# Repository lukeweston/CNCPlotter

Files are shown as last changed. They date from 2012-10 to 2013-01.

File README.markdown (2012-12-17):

CNCPlotter

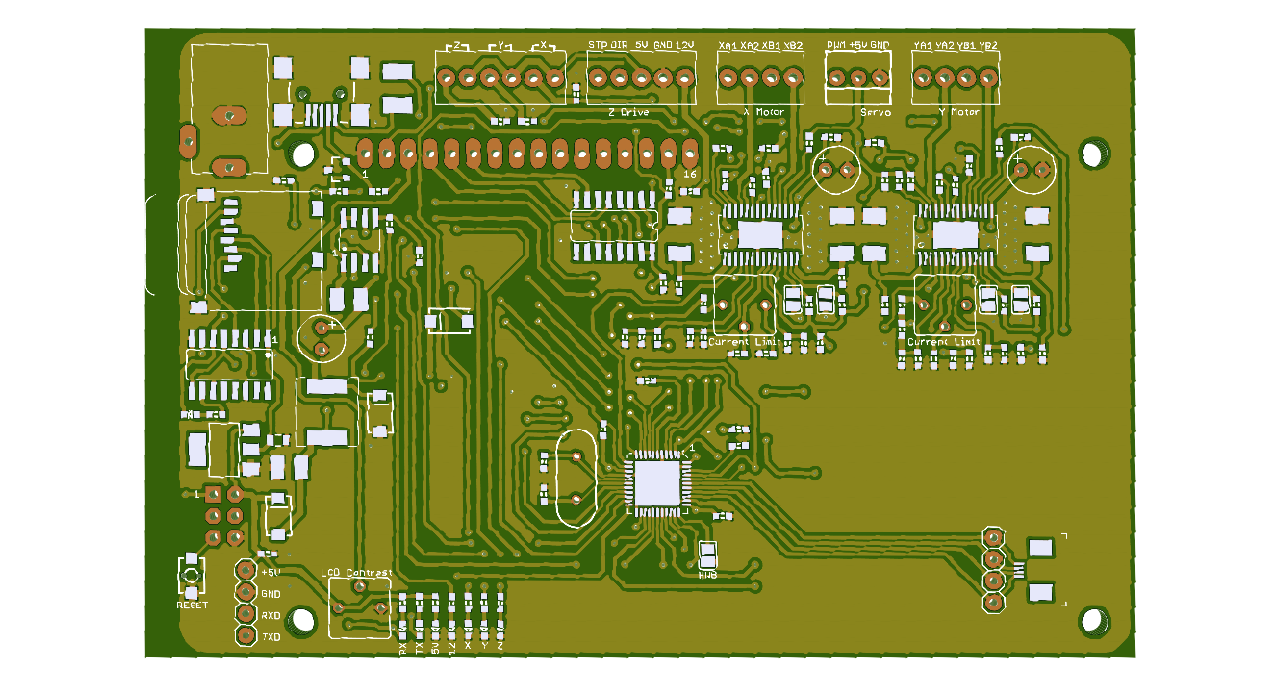
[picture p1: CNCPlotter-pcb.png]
 

The Freetronics CNCPlotter board is an Arduino-compatible embedded machine which incorporates two bipolar stepper motor drivers, suitable for CNC experiments and other
robotics and mechatronics applications.

The board incorporates the following hardware features:
 
- Atmel ATmega32U4 microcontroller, compatible with the Arduino Leonardo firmware, and USB connectivity to the PC. 
- 20x4 HD44780-compatible alphanumeric LCD display 
- Micro-SD card socket, for example usable for the execution of stored programs without connection to a PC. 
- Connector for a small (hobby RC aircraft style) servo motor 
- Two onboard DRV8811 bipolar stepper motor driver ICs 
- Inputs for three "limit" or "home" switches (or switches with any other kind of software-defined functionality!) 
- Connector for a cheap 4-wire resistive touchscreen, such as a Nintendo DS compatible touchscreen 
- Power supply input voltage range of 9-30V. (At least 1A current capacity is required to run the stepper motors.) 
- Output header for an optional third stepper motor driver IC, enabling three-axis CNC applications. 

Assuming you're using an Arduino Leonardo bootloader, the following is the mapping of Arduino pins to hardware functions.	

D0: UART RXD (not used, broken out to spare header) 	
D1: UART TXD (not used, broken out to spare header) 	
D2: LCD Strobe (Data loaded serially from AVR into 8-bit latch. Same as Pebble LCD hardware.) 	
D3: LCD Data 	
D4: LCD Clock 	
D5: Z-axis direction (not used in most cases) 	
D6: SD Card SPI chip select (active low). Standard SPI hardware (MOSI, MISO, SCK) used for SPI communications with SD card. 	
D7: Z-axis limit switch input (not used in most cases) 	
D8: Y-axis step signal 	
D9: Y-axis direction signal 	
D10: X-axis step signal 	
D11: X-axis direction signal 	
D12: Servo motor PWM position signal 	
D13: Z-axis step signal (not used usually) 	

A0: Touchscreen 1 	
A1: Touchscreen 2 	
A2: Touchscreen 3 	
A3: Touchscreen 4 	
A4: Y-axis limit switch input 	
A5: X-axis limit switch input

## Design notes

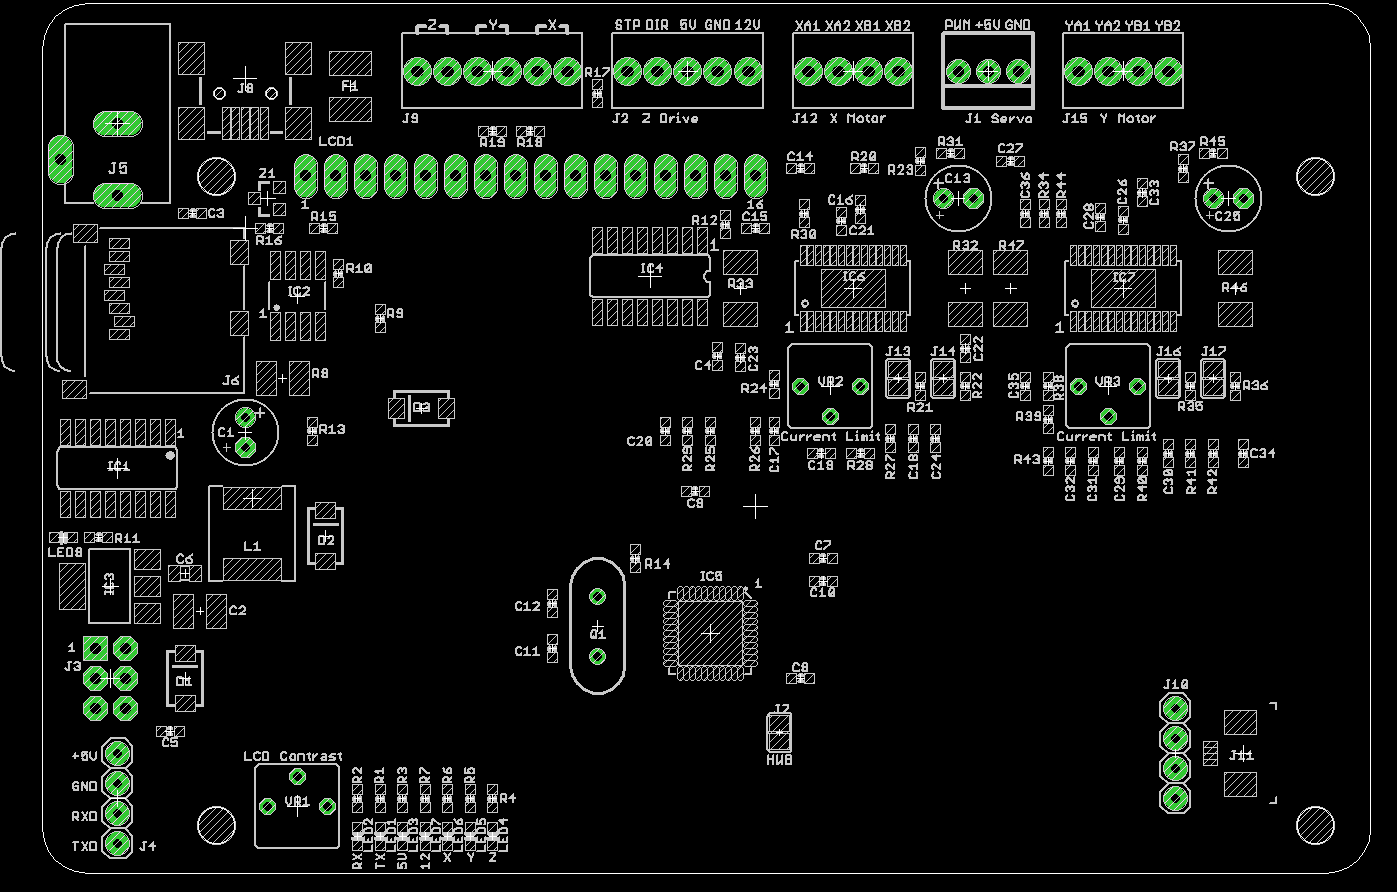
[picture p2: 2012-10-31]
CNCPlotter-placement.png

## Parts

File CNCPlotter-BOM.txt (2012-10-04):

R1, R2, R3, R4, R5, R6, R9, R11:								1k0, 0.1W, 0603 SMD, 5%
R13, R14, R17, R18, R19, R20, R21, R22, R23, R25, R30, R31, R34, R35, R36, R37, R39, R44, R45:	10k, 0.1W, 0603 SMD, 5%

R10:			3k0, 0.1W, 0603 SMD, 1%
R24, R38:		3k3, 0.1W, 0603 SMD, 5%
R12, R15, R16:		22R, 0.1W, 0603 SMD, 5%
R26, R27, R40, R41:	47k, 0.1W, 0603 SMD, 5%
R7, R29, R43:		4k7, 0.1W, 0603 SMD, 5%
R28, R42:		0 ohm, 0603 SMD
R8:			0.20 ohms, 0.5W, 1210 SMD, 5%. Eg. Digi-Key 73L5R20JCT-ND
R32, R33, R46, R47:	0.20 ohms, 1W, 2010 SMD, 1%. Eg. Digi-Key CSRN2010FKR200CT-ND

VR1, VR2, VR3:		CT6EP103 10k trimpot, eg. Digi-Key CT6EP103-ND

C1, C13, C25:		100 uF 35V Al electrolytic, through-hole, 2.5mm lead pitch / 6mm diameter. Eg. Digi-Key 399-6104-ND
C2:			47 uF ceramic, 1210 SMD. Eg. Digi-Key 445-1409-1-ND
C6:			10uF ceramic, 0805 SMD. Eg. Digi-Key 445-1371-1-ND
C3:			100 pF ceramic, 0603 SMD.
C9:			1 uF ceramic, 0603 SMD.
C11, C12:		22 pF ceramic, 0603 SMD.
C17, C18, C29, C30:	1 nF ceramic, 0603 SMD.

C14, C16, C21, C26, C28, C33:	220nF ceramic, 0603 SMD
C4, C5, C7, C8, C10, C15, C19, C20, C22, C23, C24, C27, C31, C32, C34, C35, C36: 100nF ceramic, 0603 SMD

D1, D2, D3:	CDBA120 Schottky diode, SMA package. Eg. Digi-Key 641-1014-1-ND
Z1:		PGB102ST23 ESD supressor, eg. Digi-Key F2596CT-ND 
Q1:		16 MHz crystal, through-hole HC-49US. Eg. Digi-Key 631-1108-ND
L1:		CR75 33uH power inductor, eg. Digi-Key 308-1539-1-ND
F1:		500mA PPTC, 1812 SMD package. Eg. Digi-Key 507-1361-1-ND

IC1:		MC14050, 16-SOIC package. Eg. Digi-Key MC14050BDGOS-ND
IC2:		MC34063 switching regulator, 8-SOIC package. Eg. Digi-Key 497-7852-1-ND
IC3:		LD1117S33C 3.3V regulator, SOT-223 package. Eg. Digi-Key 497-1241-1-ND
IC4:		74HC4094 shift register, 16-SOIC package. Eg. Digi-Key 568-1465-5-ND
IC5:		ATmega32U4 AVR microcontroller, 44-QFN package. Eg. Digi-Key ATMEGA32U4-MU-ND
IC6, IC7:	DRV8811 stepper motor driver, 28-HTSSOP. Eg. Digi-Key 296-24591-1-ND

LED1, LED7:		LED, green, 0603 SMD.
LED2, LED8:		LED, yellow, 0603 SMD.
LED3:			LED, blue, 0603 SMD.
LED4, LED5, LED6:	LED, red, 0603 SMD.

J1:		3-pin 0.1" pin header
J3:		2x3 0.1" pin header
J2:		5-pin 0.1" PCB-mount screw terminal block, eg. Digi-Key A98336-ND
J5:		2.1mm DC power jack, eg. Digi-Key CP-037A-ND
J6:		Micro-SD card socket, eg. Digi-Key 101-00660-68-6-1-ND
J8:		USB Mini-B socket, eg. Digi-Key H2959CT-ND
J9:		6-pin 0.1" PCB-mount screw terminal block, eg. Digi-Key A98337-ND
J11: 		4-pin 0.5mm SMD FFC ribbon connector, eg. Digi-Key 609-4328-1-ND
J12, J15:	4-pin 0.1" PCB-mount screw terminal block, eg. Digi-Key A98335-ND
J4:		NOT PLACED.
J10: 		NOT PLACED.

LCD1:		20x4 HD44780-compatible backlit LCD display module.
Same as Pebble, RAMPS Display Board, etc etc.
Also include appropriate headers (16-pin single-row 0.1", mating male/female pair) for LCD.

Also needed: 12V plugpack.

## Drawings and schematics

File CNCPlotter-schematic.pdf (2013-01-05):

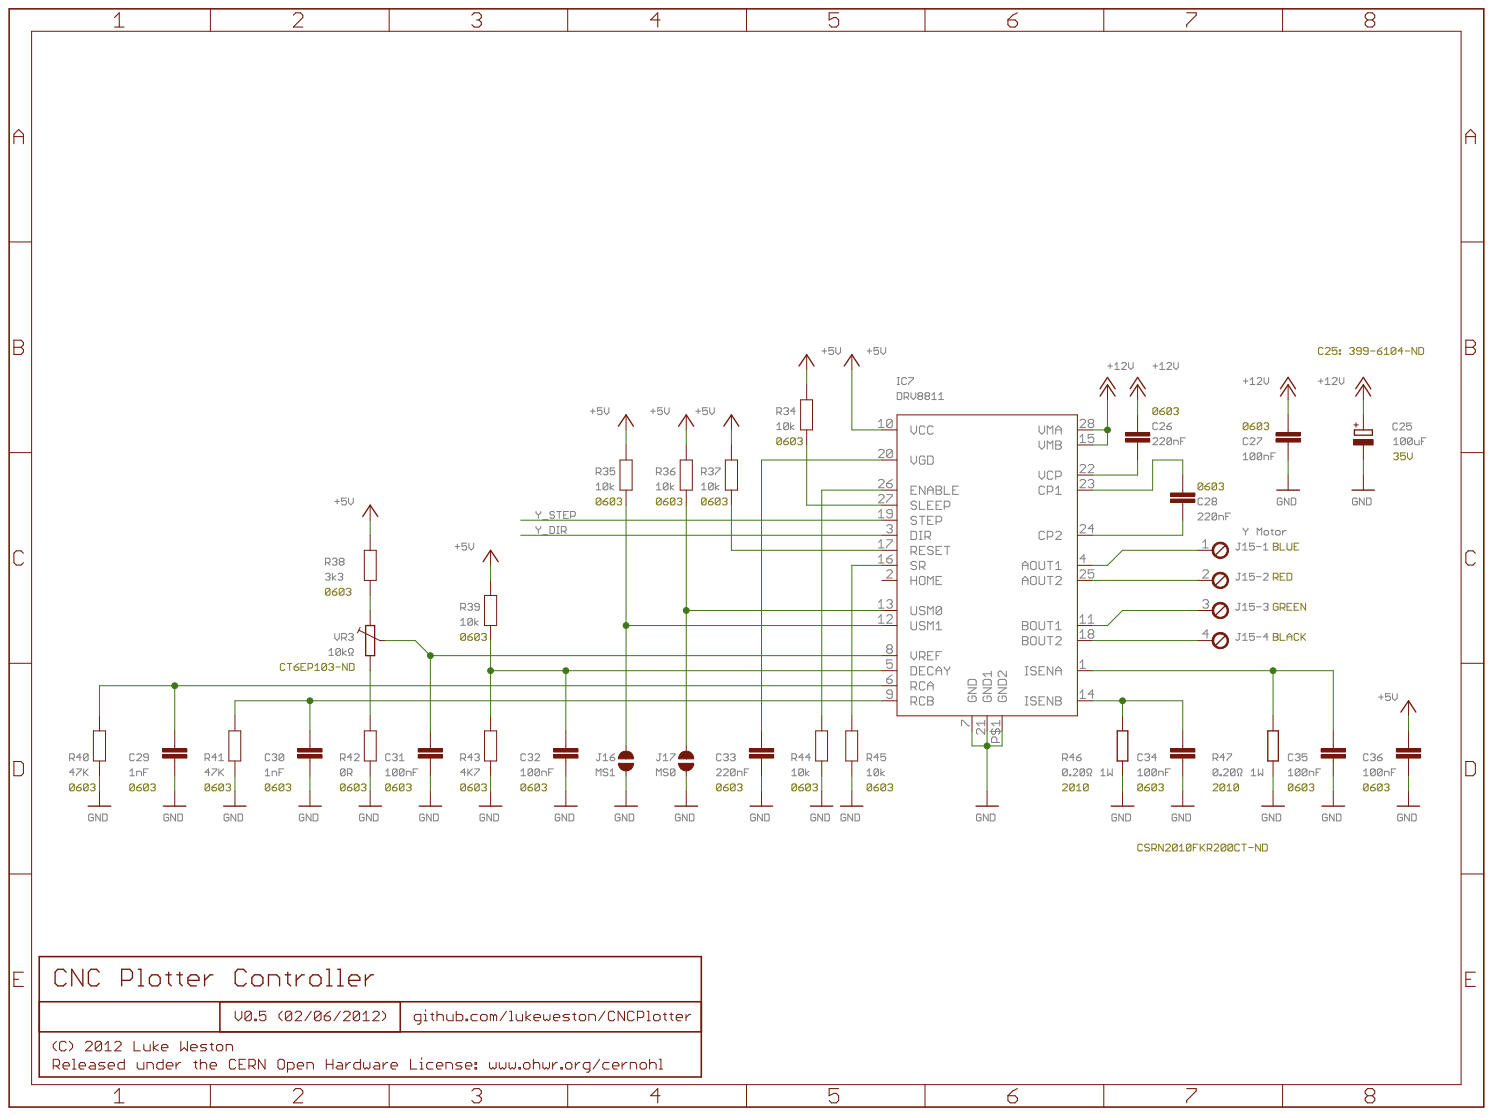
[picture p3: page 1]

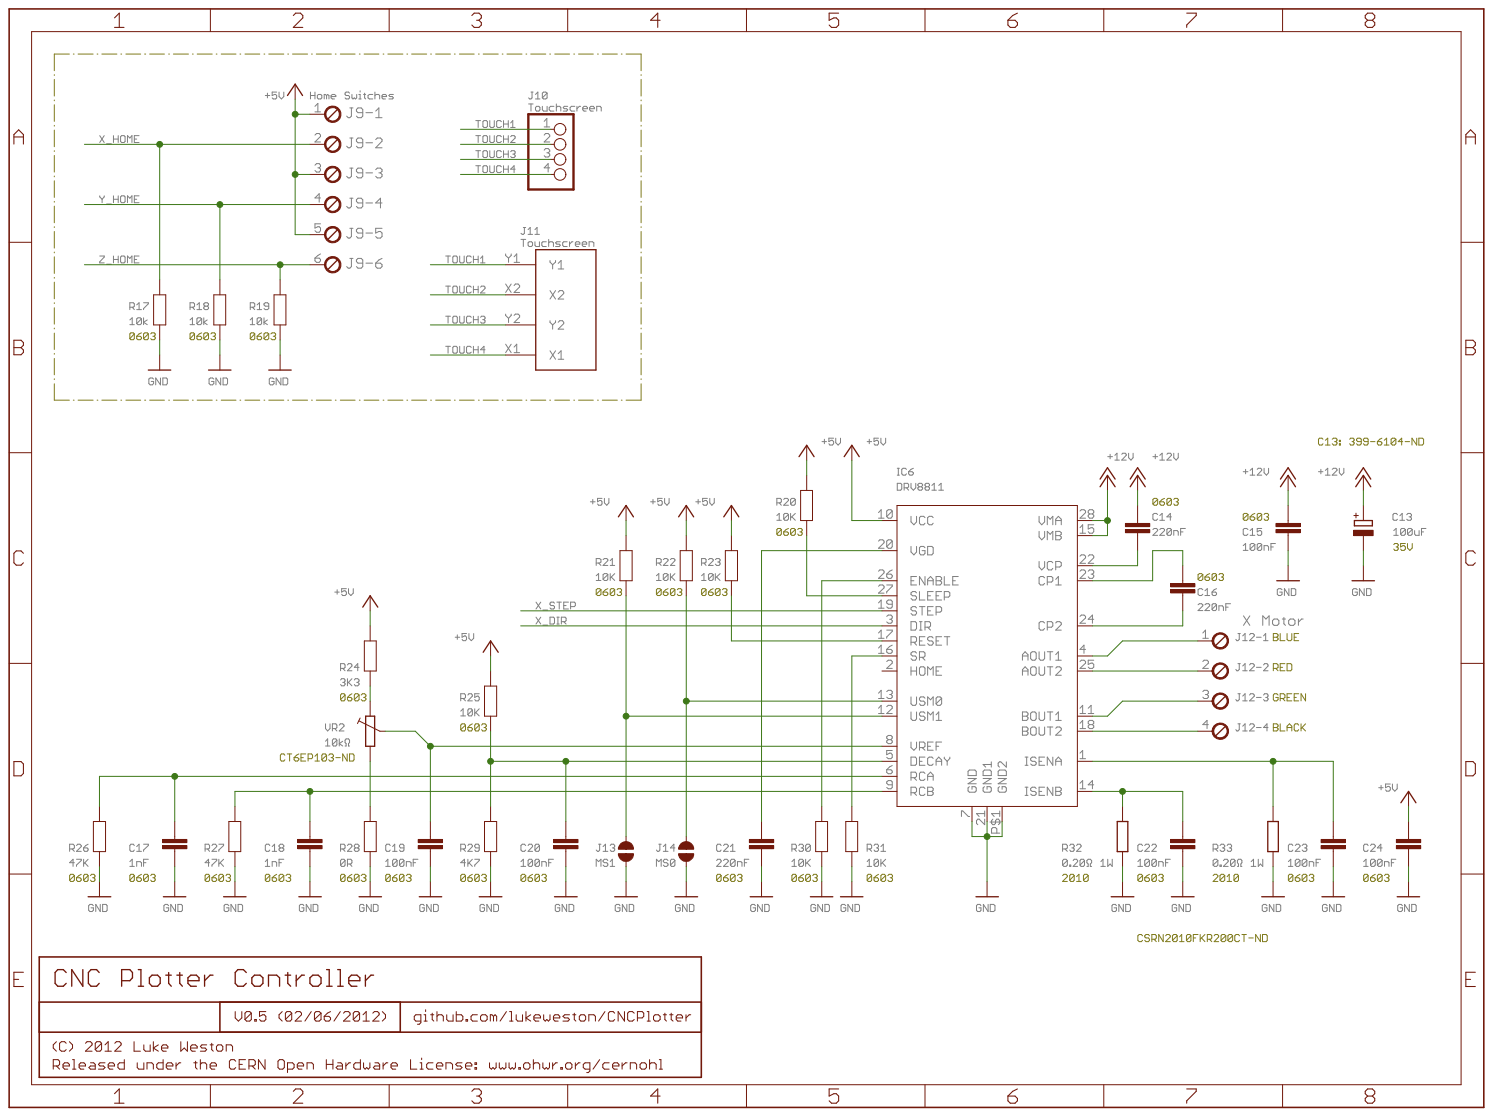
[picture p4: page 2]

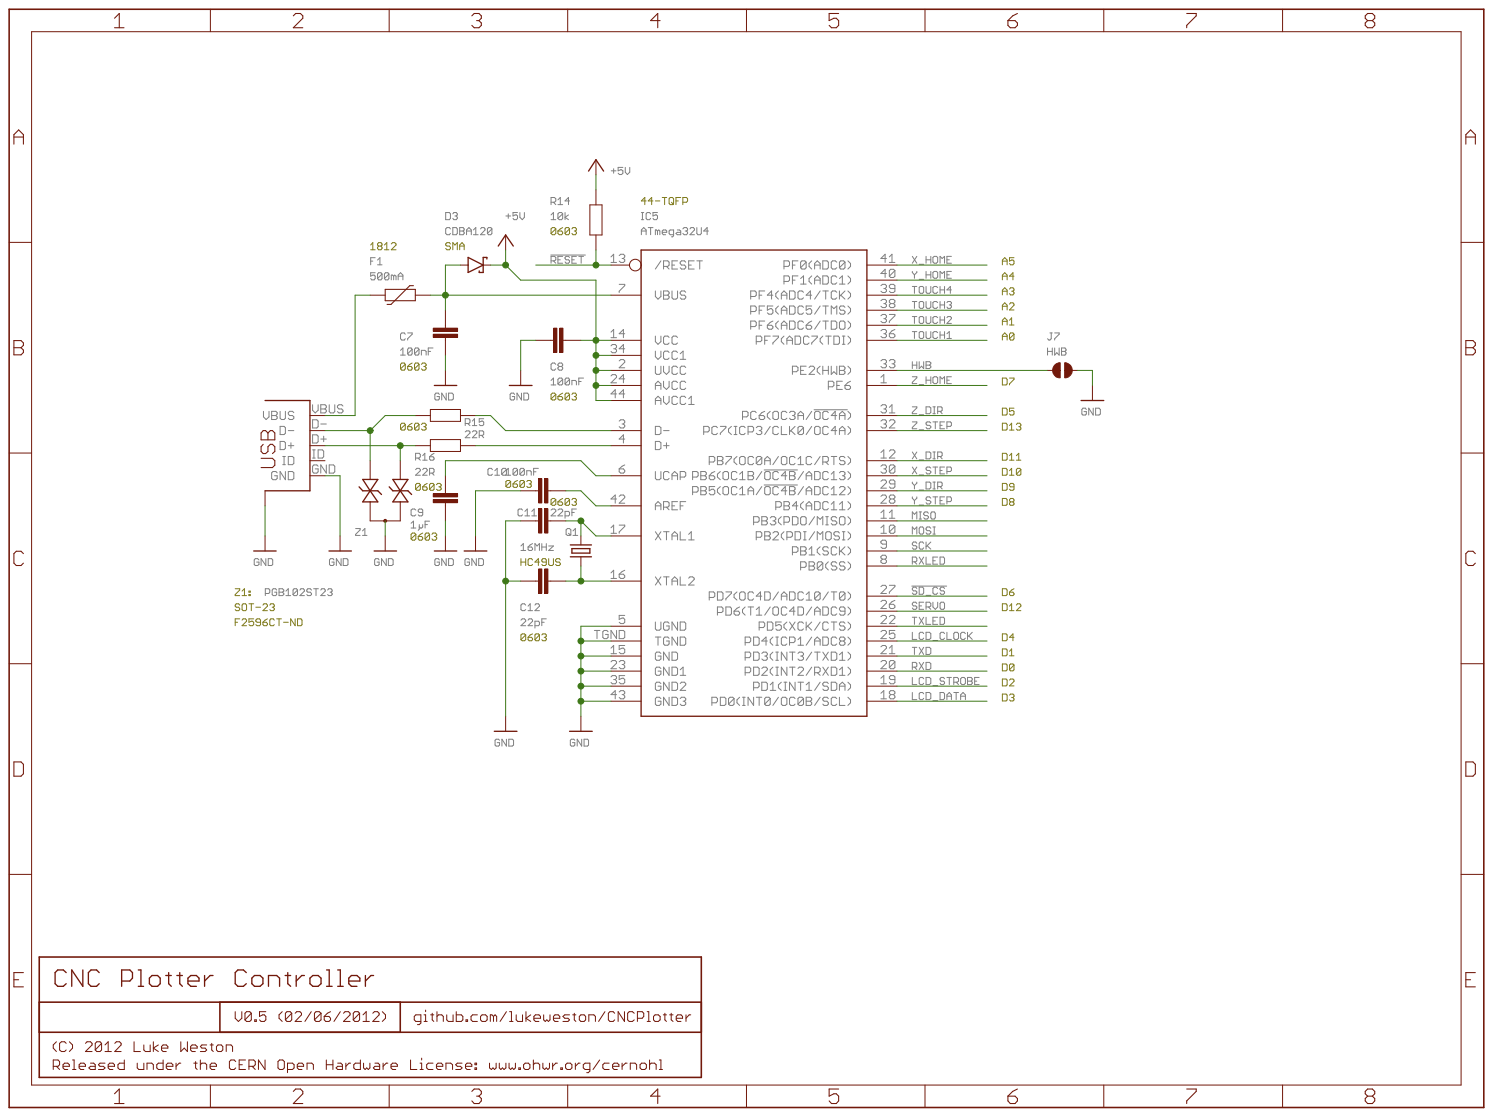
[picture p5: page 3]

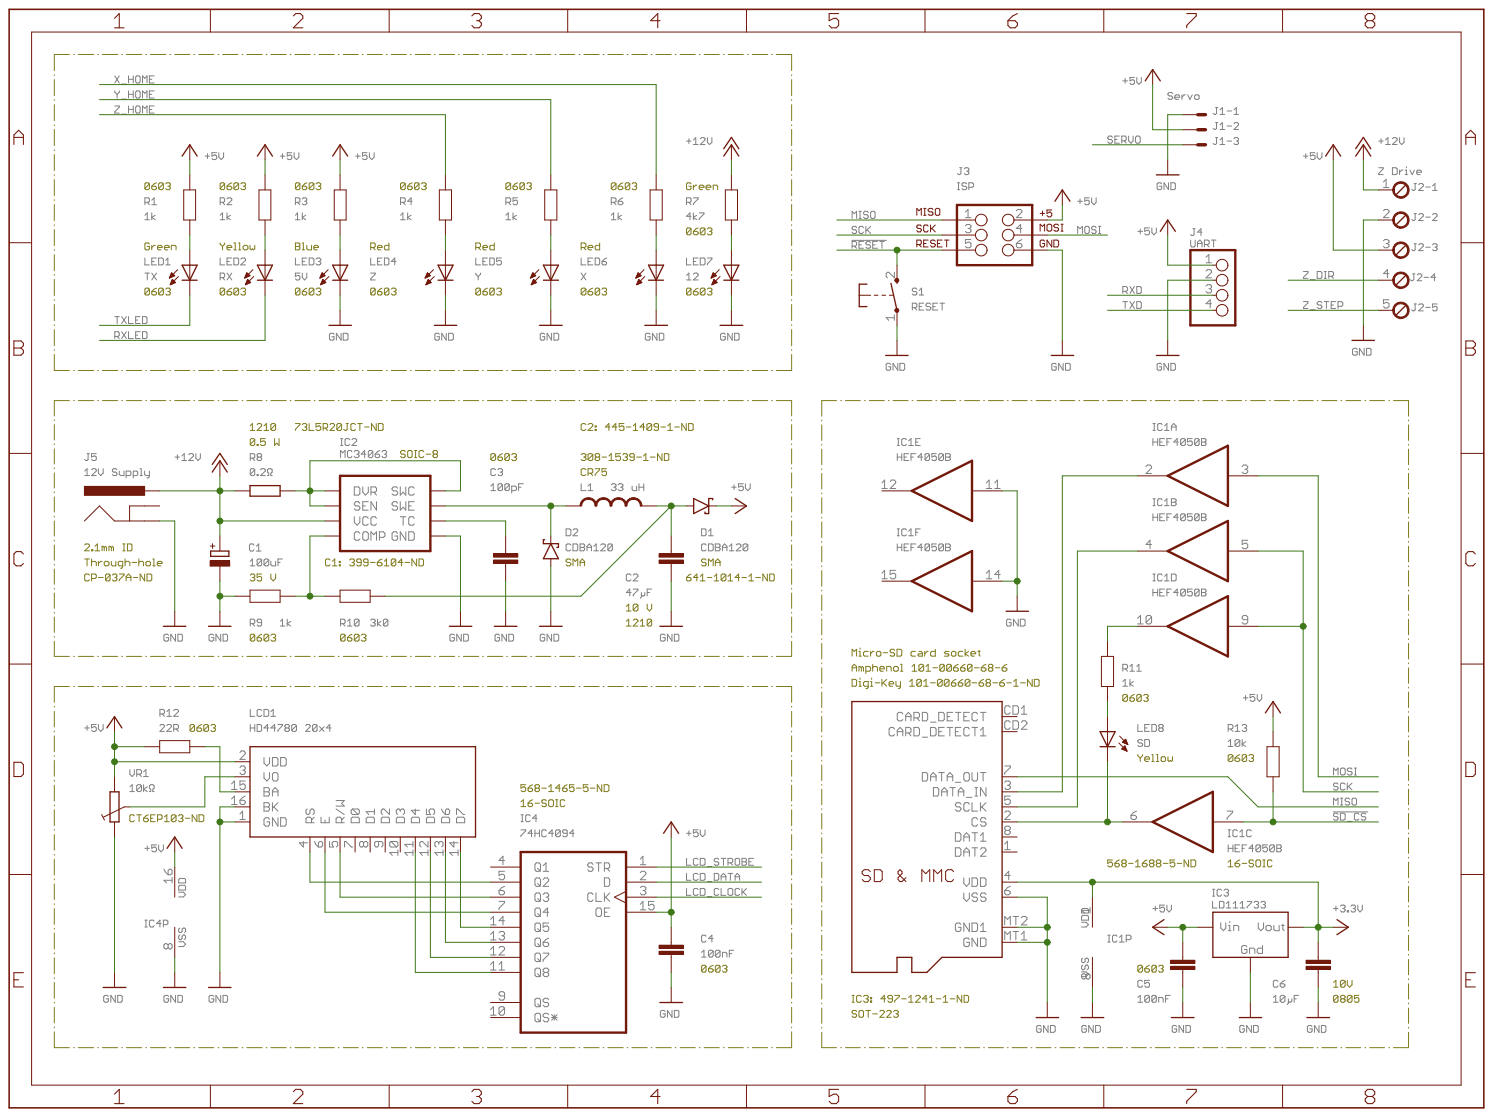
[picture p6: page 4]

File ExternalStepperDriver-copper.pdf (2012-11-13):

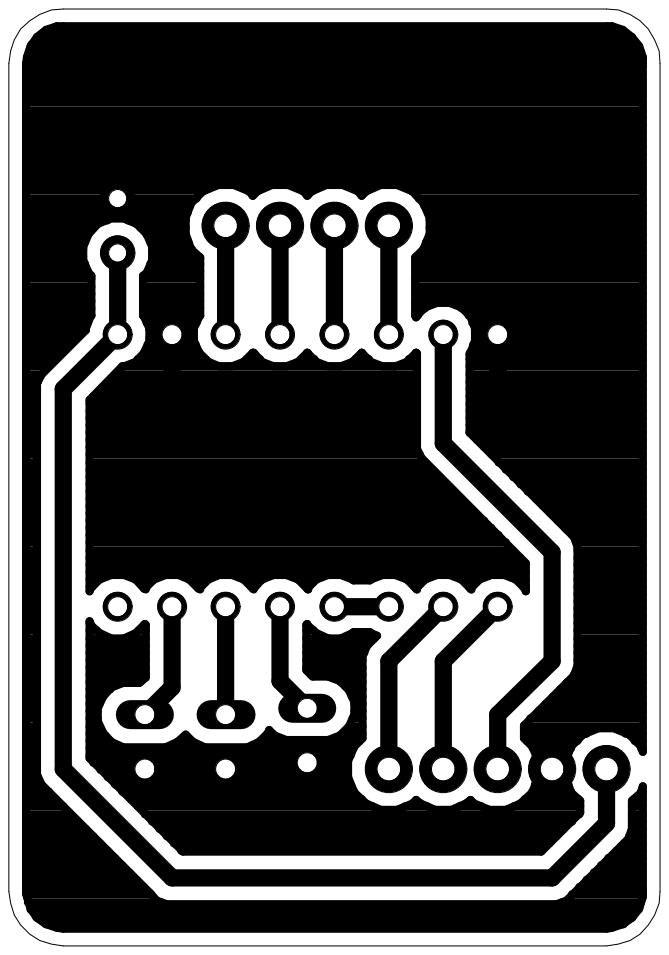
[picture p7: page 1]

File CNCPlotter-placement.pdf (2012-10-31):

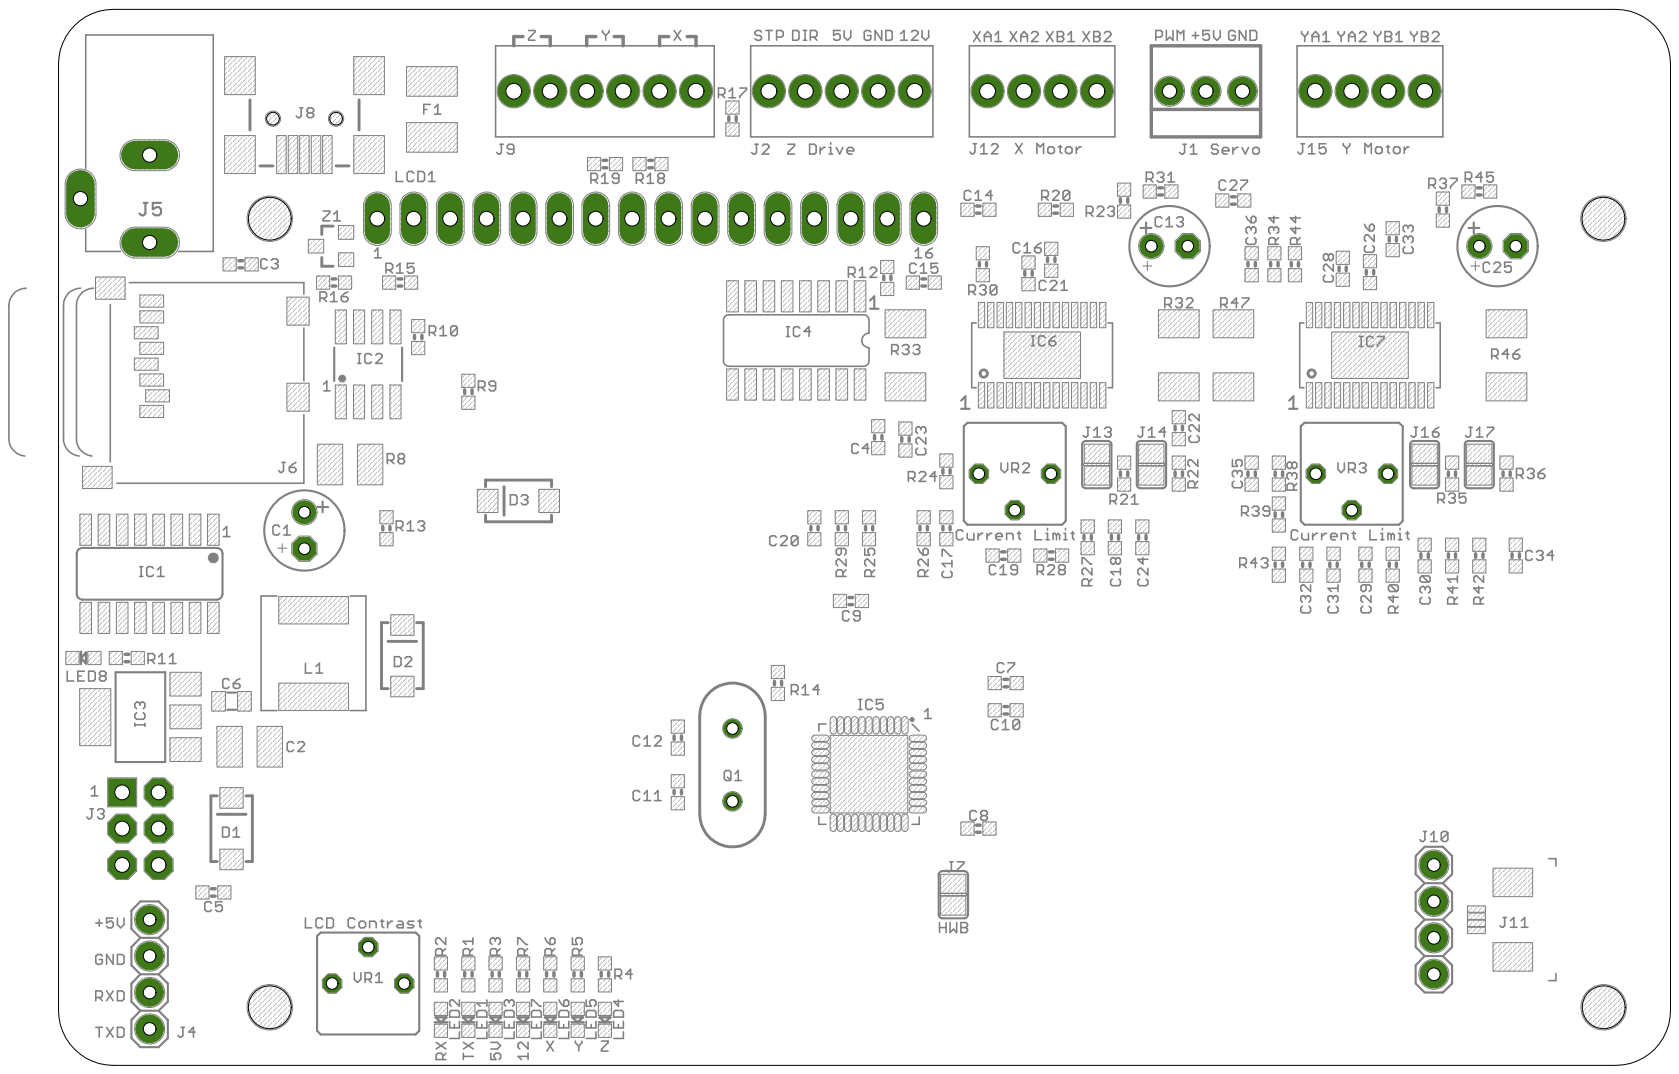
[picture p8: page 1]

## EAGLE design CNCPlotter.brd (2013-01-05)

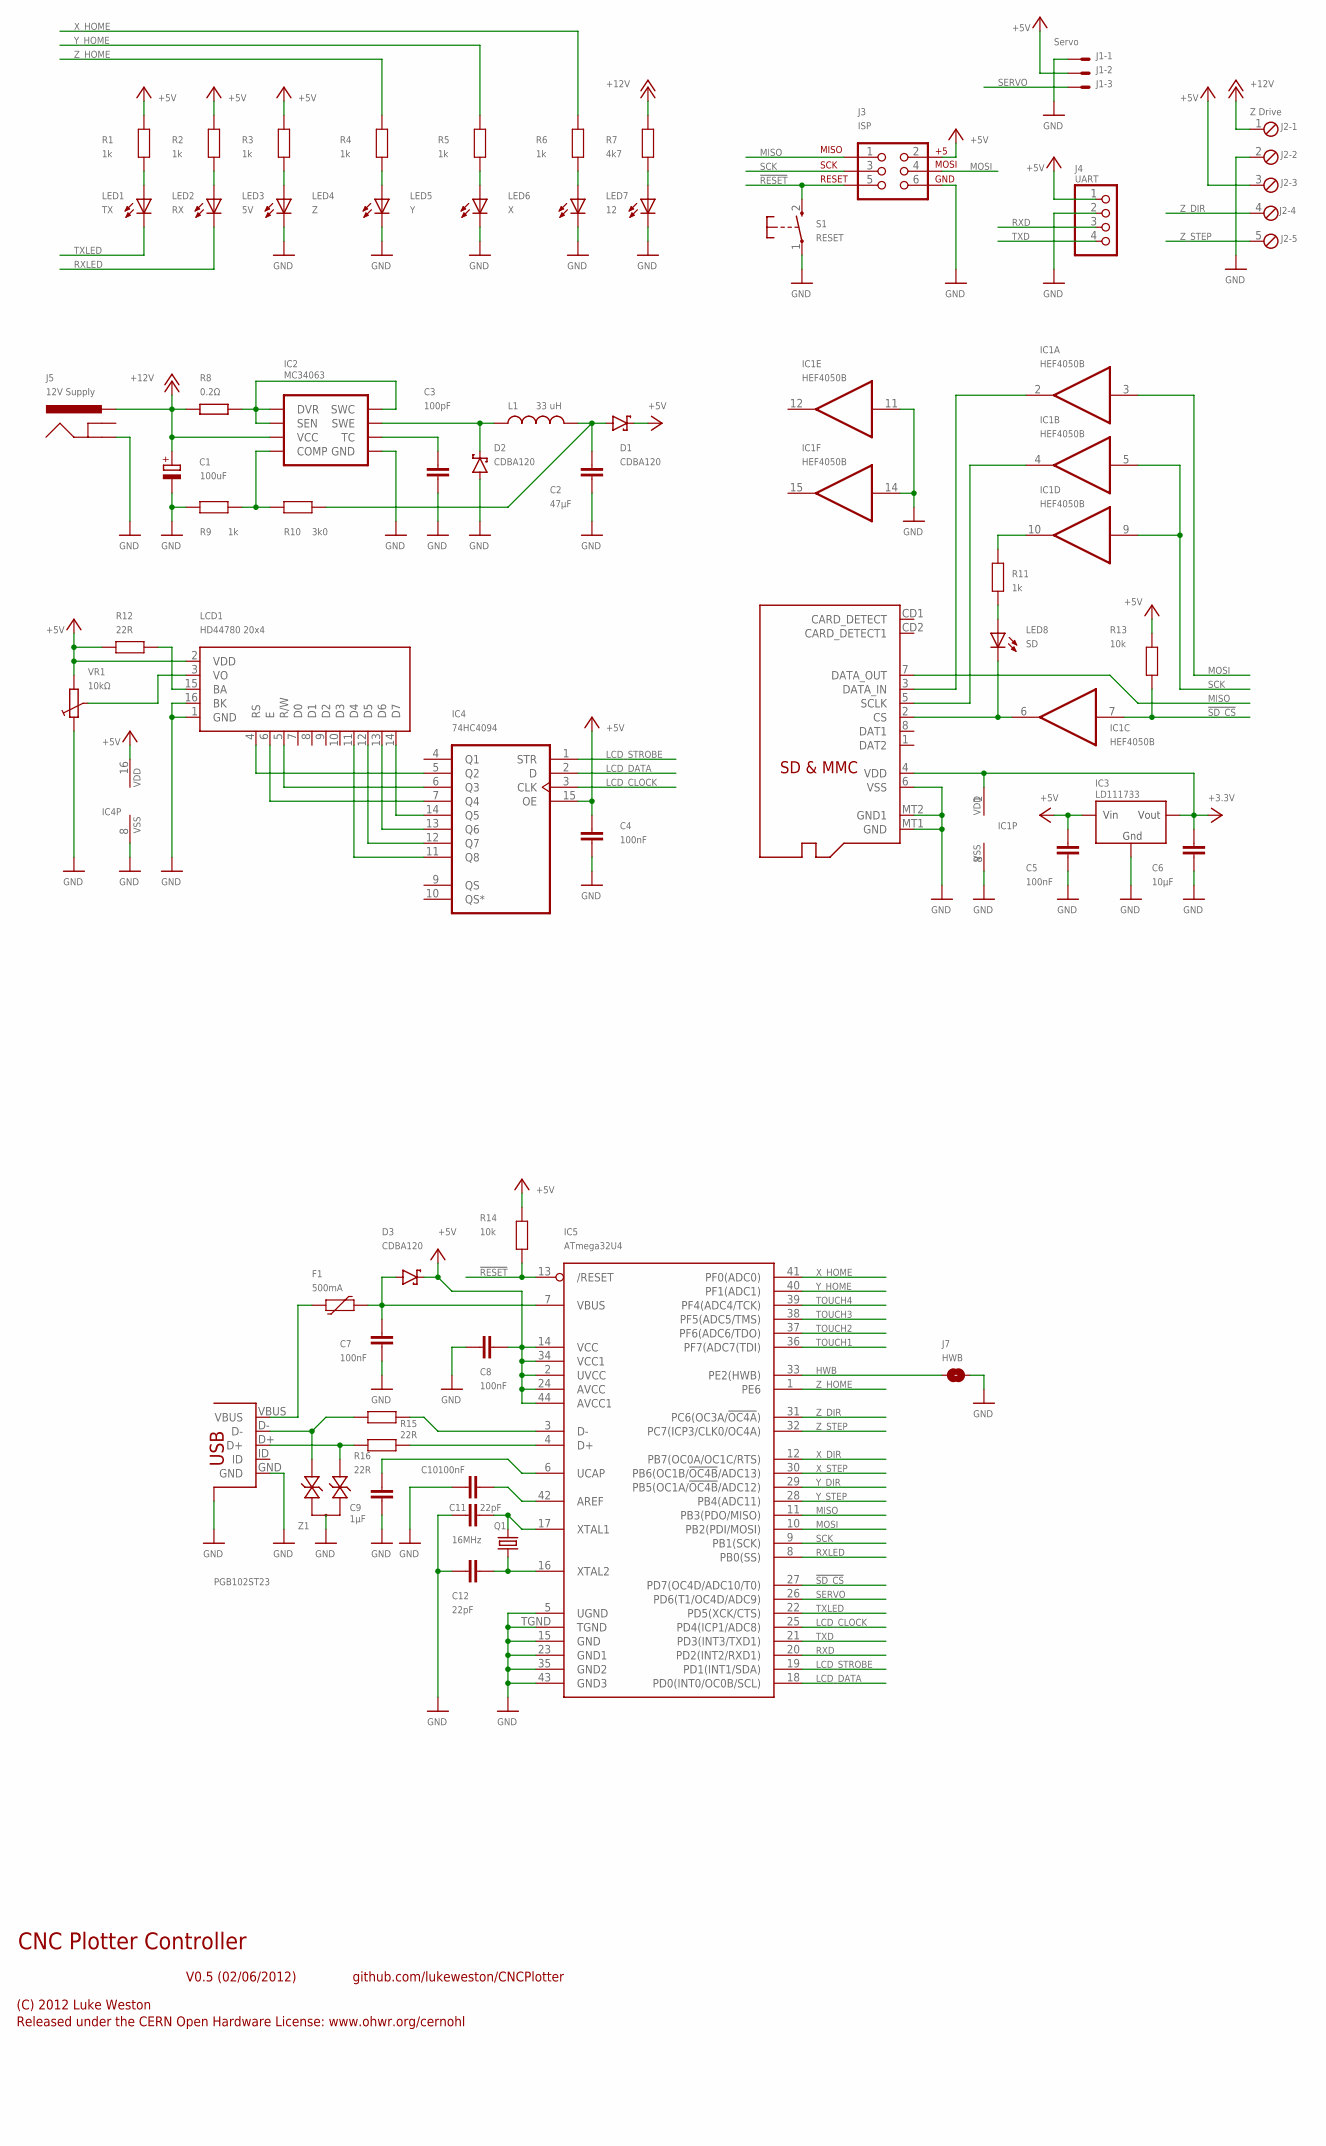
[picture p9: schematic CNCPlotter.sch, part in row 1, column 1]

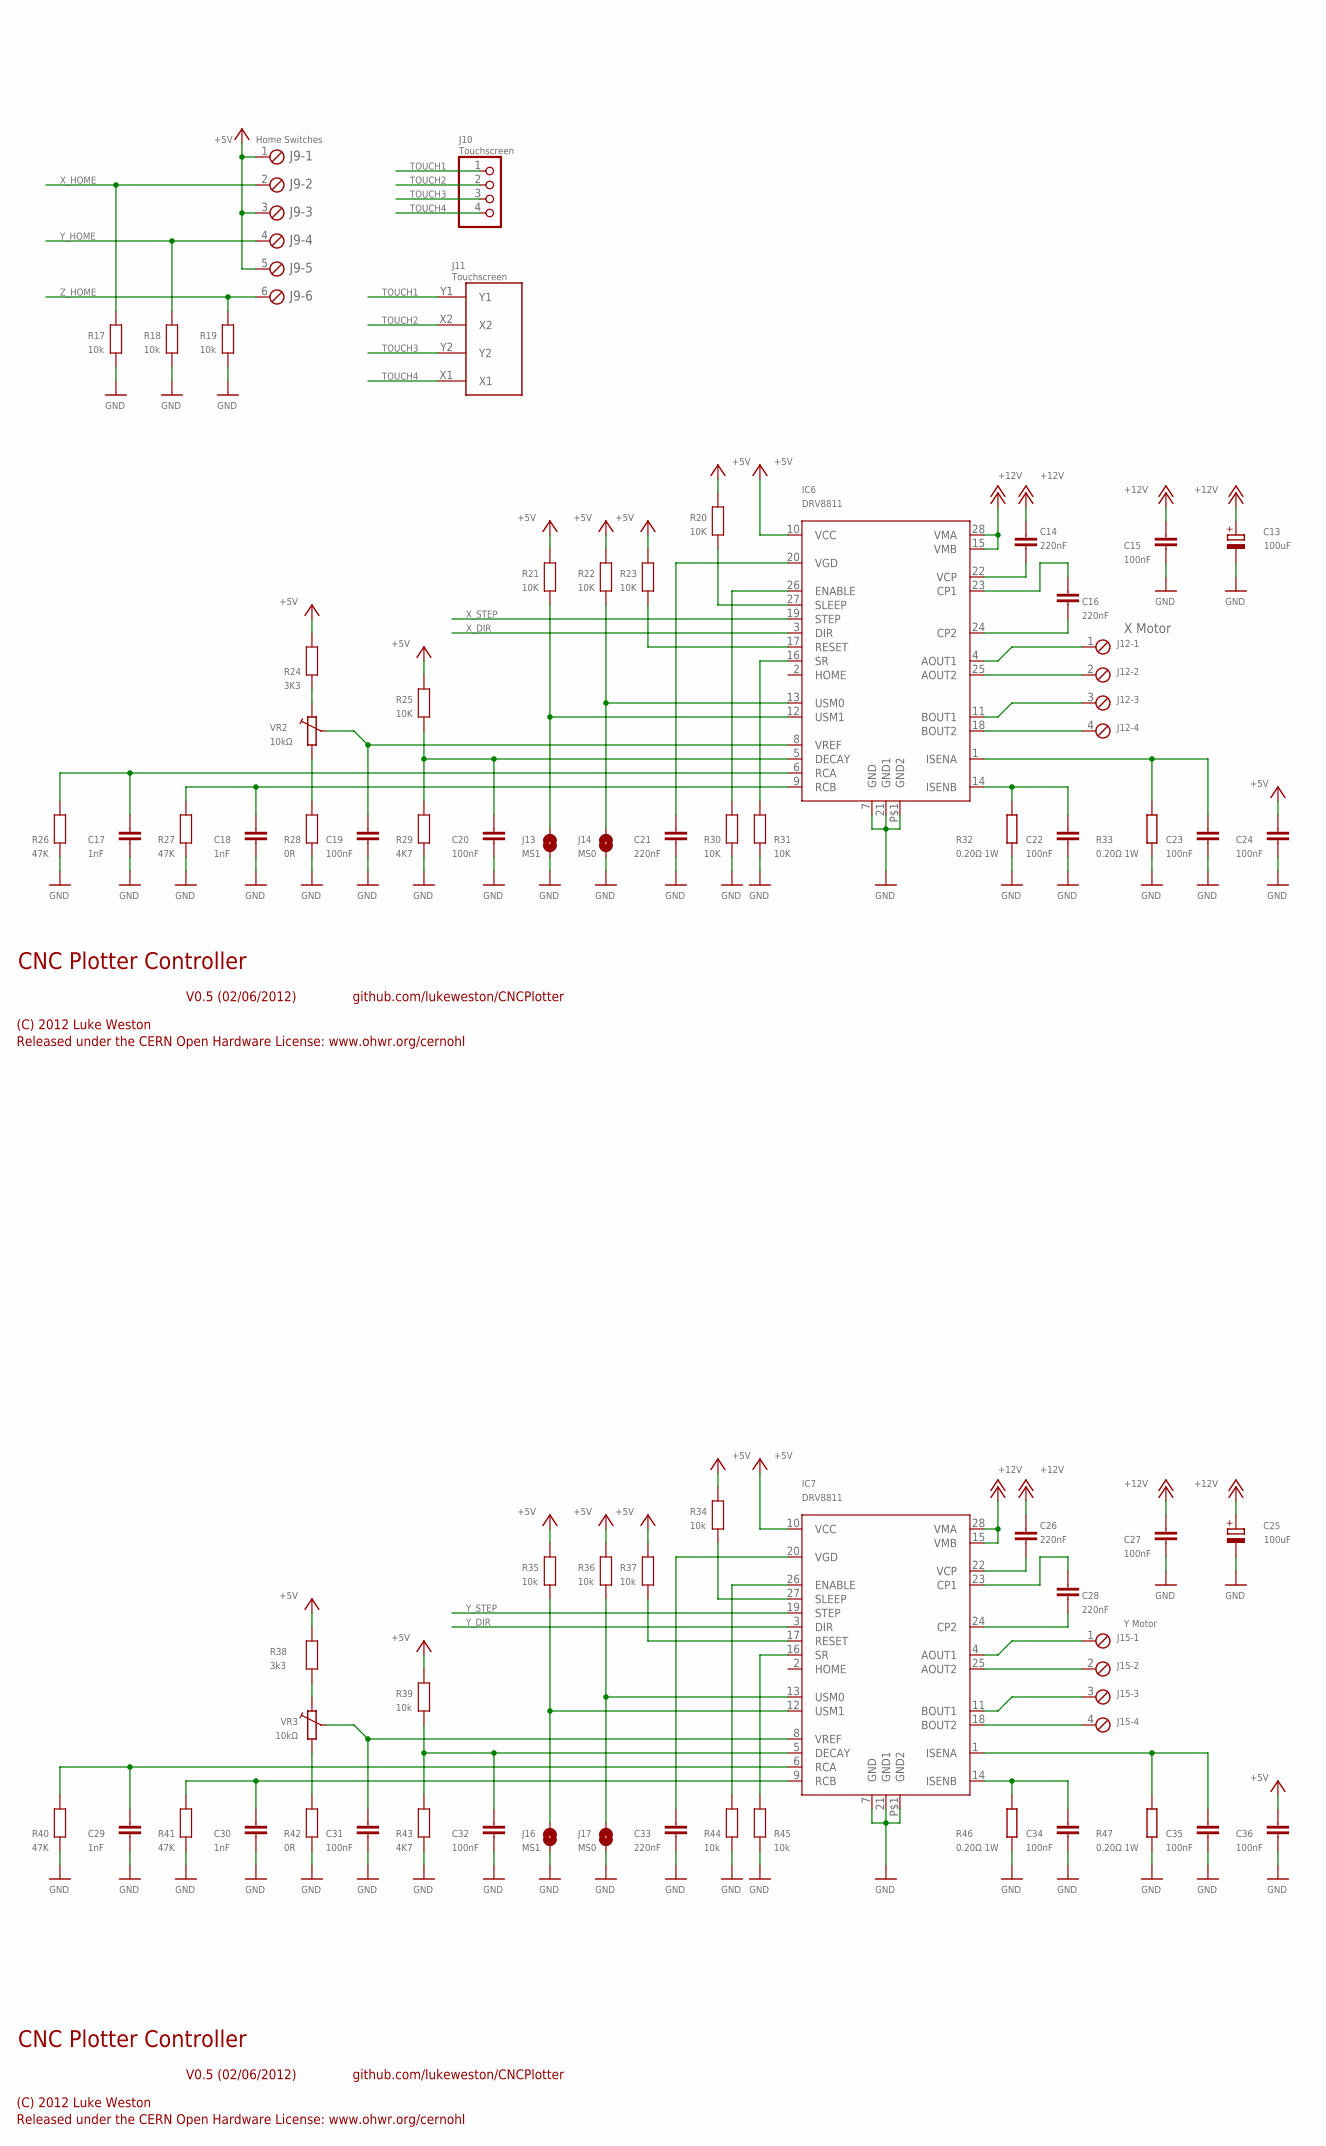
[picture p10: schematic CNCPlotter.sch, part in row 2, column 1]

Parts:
C1, C13, C25: 100uF; E2,5-6
C2: 47µF; C1210
C3: 100pF; 0603
C4, C5, C7, C8, C10, C15, C19, C20, C22, C23, C24, C27, C31, C32, C34, C35, C36: 100nF; 0603
C6: 10µF; 0805
C9: 1µF; 0603
C11, C12: 22pF; 0603
C14, C16, C21, C26, C28, C33: 220nF; 0603
C17, C18, C29, C30: 1nF; 0603
D1, D2, D3: CDBA120; SMA
F1: 500mA; 1812
IC1: HEF4050B; SO16
IC2: MC34063; SO08
IC3: LD111733; SOT223
IC4: 74HC4094; SO16@1
IC5: ATmega32U4; QFN-44N
IC6, IC7: DRV8811; HTSSOP28
J1: Servo; 22-23-2031
J2: Z Drive; 5POL254
J3: ISP; 2X3-NS
J4: UART; 1X04
J5: 12V Supply; POWER_JACK_SLOT
J6: MicroSD Card; ADAFRUIT_MICROSD
J7: HWB; SJ
J8: USB; USB-MINIB-FT
J9: Home Switches; 6POL254
J10: Touchscreen; 1X04
J11: Touchscreen; DS_TOUCH_CONNECTOR
J12: X Motor; 4POL254
J13, J16: MS1; SJ
J14, J17: MS0; SJ
J15: Y Motor; 4POL254
L1: 33 uH; CR75
LCD1: HD44780 20x4; HDM20416L
LED1: TX; LED-0603
LED2: RX; LED-0603
LED3: 5V; LED-0603
LED4: Z; LED-0603
LED5: Y; LED-0603
LED6: X; LED-0603
LED7: 12; LED-0603
LED8: SD; LED-0603
Q1: 16MHz; HC49US
R1, R2, R3, R4, R5, R6, R9, R11: 1k; 0603
R7: 4k7; 0603
R8: 0.2Ω; R1210
R10: 3k0; 0603
R12, R15, R16: 22R; 0603
R13, R14, R17, R18, R19, R34, R35, R36, R37, R39, R44, R45: 10k; 0603
R20, R21, R22, R23, R25, R30, R31: 10K; 0603
R24: 3K3; 0603
R26, R27, R40, R41: 47K; 0603
R28, R42: 0R; 0603
R29, R43: 4K7; 0603
R32, R33, R46, R47: 0.20Ω 1W; R2010
R38: 3k3; 0603
S1: RESET; TACTILE_SWITCH_SMD_2PIN_TINY
VR1, VR2, VR3: 10kΩ; CT6
Z1: PGB102ST23; SOT23-3

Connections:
!RESET: IC5.13 (/RESET), J3.5, R14.1, S1.2 (S)
!SD_CS: IC1.7 (I), IC5.27 (PD7(OC4D/ADC10/T0)), R13.1
+5V: C4.1, C5.1, C8.2, C24.1, C36.1, D1.K, D3.K, IC3.3 (VIN), IC4.15 (OE), IC4.16 (VDD), IC5.2 (UVCC), IC5.14 (VCC), IC5.24 (AVCC), IC5.34 (VCC1), IC5.44 (AVCC1), IC6.10 (VCC), IC7.10 (VCC), J1.2, J2.3, J3.2, J4.1, J9.1, J9.3, J9.5, LCD1.2 (VDD), R1.2, R2.2, R3.2, R12.2, R13.2, R14.2, R20.2, R21.2, R22.2, R23.2, R24.2, R25.2, R34.2, R35.2, R36.2, R37.2, R38.2, R39.2, VR1.A
+12V: C1.+, C13.+, C14.1, C15.1, C25.+, C26.1, C27.1, IC2.6 (VCC), IC6.15 (VMB), IC6.28 (VMA), IC7.15 (VMB), IC7.28 (VMA), J2.1, J5.PWR, R7.2, R8.1
FOO: IC1.6 (O), J6.2 (CS), LED8.C
GND: C1.-, C2.2, C3.2, C4.2, C5.2, C6.2, C7.2, C8.1, C9.1, C10.1, C11.1, C12.1, C13.-, C15.2, C17.2, C18.2, C19.2, C20.2, C21.2, C22.2, C23.2, C24.2, C25.-, C27.2, C29.2, C30.2, C31.2, C32.2, C33.2, C34.2, C35.2, C36.2, D2.A, IC1.8 (VSS), IC1.11 (I), IC1.14 (I), IC2.4 (GND), IC3.1 (GND), IC4.8 (VSS), IC5.5 (UGND), IC5.15 (GND), IC5.23 (GND1), IC5.35 (GND2), IC5.43 (GND3), IC5.TGND, IC6.7 (GND), IC6.21 (GND1), IC6.P$1 (GND2), IC7.7 (GND), IC7.21 (GND1), IC7.P$1 (GND2), J1.1, J2.2, J3.6, J4.2, J5.GND, J6.6 (VSS), J6.MT1 (GND), J6.MT2 (GND1), J7.1, J8.GND, J8.SH1 (SH$1), J8.SH2 (SH$1), J8.SH3 (SH$1), J8.SH4 (SH$1), J13.1, J14.1, J16.1, J17.1, LCD1.1 (GND), LCD1.16 (BK), LED3.C, LED4.C, LED5.C, LED6.C, LED7.C, R9.2, R17.2, R18.2, R19.2, R26.1, R27.1, R28.1, R29.1, R30.1, R31.1, R32.1, R33.1, R40.1, R41.1, R42.1, R43.1, R44.1, R45.1, R46.1, R47.1, S1.1, VR1.E, Z1.3
HWB: IC5.33 (PE2(HWB)), J7.2
LCD_CLOCK: IC4.3 (CLK), IC5.25 (PD4(ICP1/ADC8))
LCD_DATA: IC4.2 (D), IC5.18 (PD0(INT0/OC0B/SCL))
LCD_STROBE: IC4.1 (STR), IC5.19 (PD1(INT1/SDA))
MISO: IC5.11 (PB3(PDO/MISO)), J3.1, J6.7 (DATA_OUT)
MOSI: IC1.3 (I), IC5.10 (PB2(PDI/MOSI)), J3.4
MOSI_3.3V: IC1.2 (O), J6.3 (DATA_IN)
unnamed: IC7.4 (AOUT1), J15.1
unnamed: F1.1, J8.VBUS
unnamed: IC6.4 (AOUT1), J12.1
unnamed: IC7.18 (BOUT2), J15.4
unnamed: IC7.11 (BOUT1), J15.3
unnamed: IC7.25 (AOUT2), J15.2
unnamed: C28.2, IC7.24 (CP2)
unnamed: C28.1, IC7.23 (CP1)
unnamed: C26.2, IC7.22 (VCP)
unnamed: C33.1, IC7.20 (VGD)
unnamed: C10.2, IC5.42 (AREF)
unnamed: LED4.A, R4.1
unnamed: C35.1, IC7.1 (ISENA), R47.2
unnamed: C34.1, IC7.14 (ISENB), R46.2
unnamed: C32.1, IC7.5 (DECAY), R39.1, R43.2
unnamed: C29.1, IC7.6 (RCA), R40.2
unnamed: C16.2, IC6.24 (CP2)
unnamed: C16.1, IC6.23 (CP1)
unnamed: IC6.16 (SR), R31.2
unnamed: C30.1, IC7.9 (RCB), R41.2
unnamed: IC6.18 (BOUT2), J12.4
unnamed: IC6.11 (BOUT1), J12.3
unnamed: IC6.25 (AOUT2), J12.2
unnamed: C14.2, IC6.22 (VCP)
unnamed: C20.1, IC6.5 (DECAY), R25.1, R29.2
unnamed: C21.1, IC6.20 (VGD)
unnamed: C17.1, IC6.6 (RCA), R26.2
unnamed: C9.2, IC5.6 (UCAP)
unnamed: LED3.A, R3.1
unnamed: LED2.A, R2.1
unnamed: LED1.A, R1.1
unnamed: IC2.1 (SWC), IC2.7 (SEN), IC2.8 (DVR), R8.2
unnamed: J8.D+, R16.2, Z1.1
unnamed: J8.D-, R15.2, Z1.2
unnamed: C11.2, IC5.17 (XTAL1), Q1.2
unnamed: C12.2, IC5.16 (XTAL2), Q1.1
unnamed: IC5.4 (D+), R16.1
unnamed: IC5.3 (D-), R15.1
unnamed: LED5.A, R5.1
unnamed: C7.1, D3.A, F1.2, IC5.7 (VBUS)
unnamed: LED6.A, R6.1
unnamed: LED7.A, R7.1
unnamed: C3.1, IC2.3 (TC)
unnamed: IC2.5 (COMP), R9.1, R10.2
unnamed: D2.K, IC2.2 (SWE), L1.P$1 (1)
unnamed: C23.1, IC6.1 (ISENA), R33.2
unnamed: C22.1, IC6.14 (ISENB), R32.2
unnamed: C18.1, IC6.9 (RCB), R27.2
unnamed: IC6.27 (SLEEP), R20.1
unnamed: IC4.5 (Q2), LCD1.4 (RS)
unnamed: IC4.6 (Q3), LCD1.5 (R/W)
unnamed: IC4.7 (Q4), LCD1.6 (E)
unnamed: IC4.11 (Q8), LCD1.11 (D4)
unnamed: IC4.12 (Q7), LCD1.12 (D5)
unnamed: IC4.13 (Q6), LCD1.13 (D6)
unnamed: IC4.14 (Q5), LCD1.14 (D7)
unnamed: IC6.17 (RESET), R23.1
unnamed: LCD1.3 (VO), VR1.S
unnamed: LCD1.15 (BA), R12.1
unnamed: R24.1, VR2.E
unnamed: R28.2, VR2.A
unnamed: LED8.A, R11.1
unnamed: IC1.10 (O), R11.2
unnamed: C19.1, IC6.8 (VREF), VR2.S
unnamed: IC6.26 (ENABLE), R30.2
unnamed: IC6.12 (USM1), J13.2, R21.1
unnamed: IC6.13 (USM0), J14.2, R22.1
unnamed: IC7.27 (SLEEP), R34.1
unnamed: IC7.17 (RESET), R37.1
unnamed: R38.1, VR3.E
unnamed: R42.2, VR3.A
unnamed: C31.1, IC7.8 (VREF), VR3.S
unnamed: IC7.26 (ENABLE), R44.2
unnamed: IC7.12 (USM1), J16.2, R35.1
unnamed: IC7.13 (USM0), J17.2, R36.1
unnamed: IC7.16 (SR), R45.2
REG_5V: C2.1, D1.A, L1.P$2 (2), R10.1
RXD: IC5.20 (PD2(INT2/RXD1)), J4.3
RXLED: IC5.8 (PB0(SS)), LED2.C
SCK: IC1.5 (I), IC1.9 (I), IC5.9 (PB1(SCK)), J3.3
SCK_3.3V: IC1.4 (O), J6.5 (SCLK)
SERVO: IC5.26 (PD6(T1/OC4D/ADC9)), J1.3
TOUCH1: IC5.36 (PF7(ADC7(TDI)), J10.1, J11.Y1
TOUCH2: IC5.37 (PF6(ADC6/TDO)), J10.2, J11.X2
TOUCH3: IC5.38 (PF5(ADC5/TMS)), J10.3, J11.Y2
TOUCH4: IC5.39 (PF4(ADC4/TCK)), J10.4, J11.X1
TXD: IC5.21 (PD3(INT3/TXD1)), J4.4
TXLED: IC5.22 (PD5(XCK/CTS)), LED1.C
VDD: C6.1, IC1.1 (VDD), IC3.2 (VOUT), J6.4 (VDD)
X_DIR: IC5.12 (PB7(OC0A/OC1C/RTS)), IC6.3 (DIR)
X_HOME: IC5.41 (PF0(ADC0)), J9.2, R6.2, R17.1
X_STEP: IC5.30 (PB6(OC1B/!OC4B!/ADC13)), IC6.19 (STEP)
Y_DIR: IC5.29 (PB5(OC1A/!OC4B!/ADC12)), IC7.3 (DIR)
Y_HOME: IC5.40 (PF1(ADC1)), J9.4, R5.2, R18.1
Y_STEP: IC5.28 (PB4(ADC11)), IC7.19 (STEP)
Z_DIR: IC5.31 (PC6(OC3A/!OC4A!)), J2.4
Z_HOME: IC5.1 (PE6), J9.6, R4.2, R19.1
Z_STEP: IC5.32 (PC7(ICP3/CLK0/OC4A)), J2.5

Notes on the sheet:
CNC Plotter Controller
V0.5 (02/06/2012)
(C) 2012 Luke Weston
Released under the CERN Open Hardware License: www.ohwr.org/cernohl
github.com/lukeweston/CNCPlotter

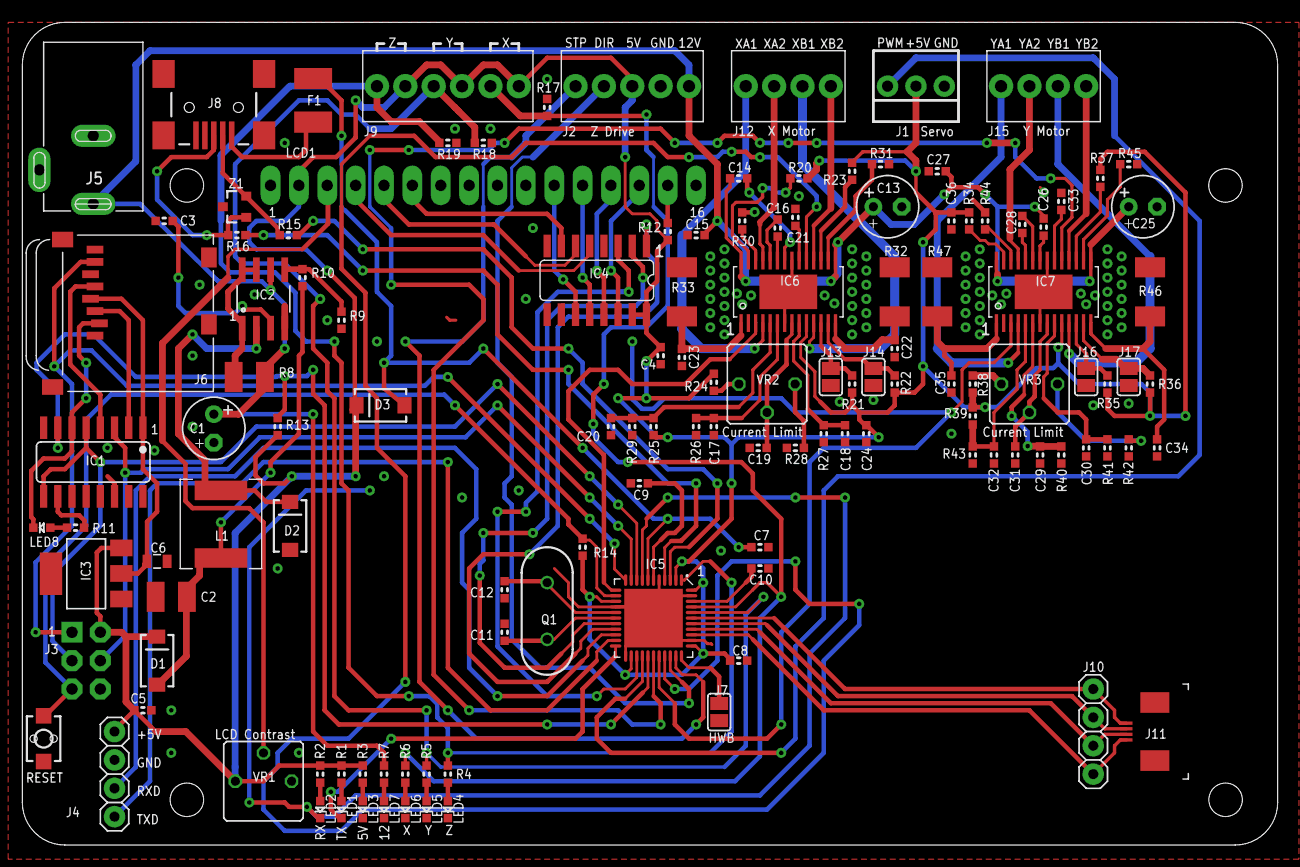
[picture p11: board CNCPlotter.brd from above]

Board: 2 copper layers, 112.4 x 73.7 mm, 127 parts (0 on the bottom side), 111 nets.

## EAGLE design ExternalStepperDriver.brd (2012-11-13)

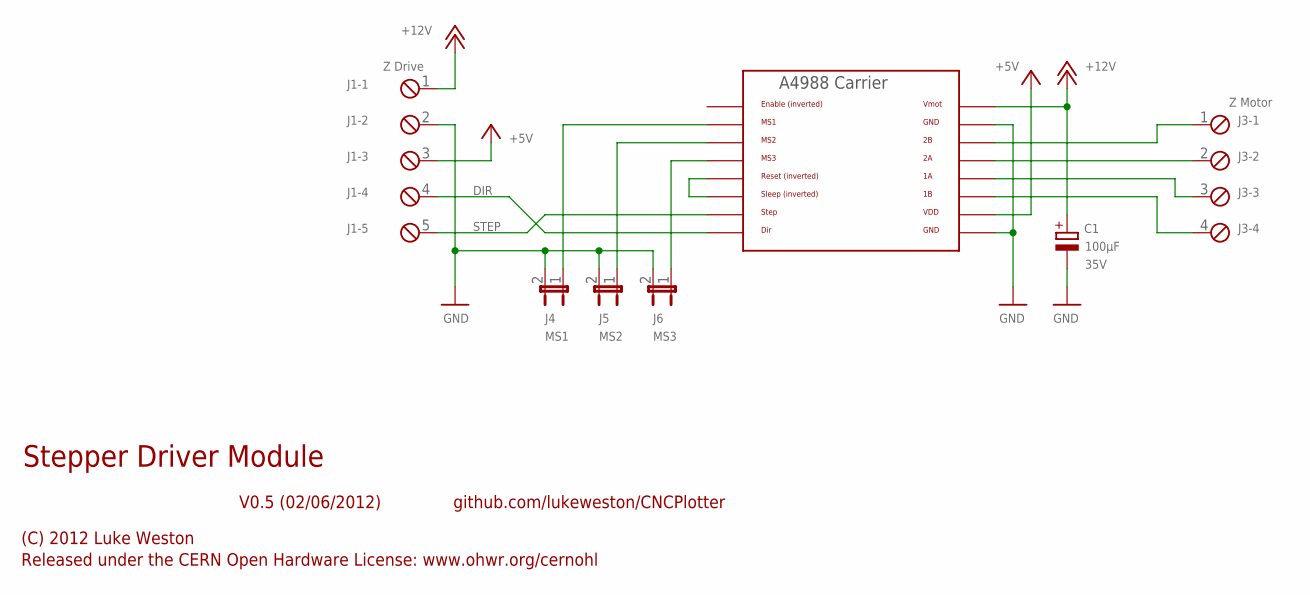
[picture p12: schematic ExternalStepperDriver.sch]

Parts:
C1: 100µF; E2,5-6; VOLTAGE 35V
J1: Z Drive; 5POL254
J2: A4988BREAKOUT
J3: Z Motor; 4POL254
J4: MS1; JP1
J5: MS2; JP1
J6: MS3; JP1

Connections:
+5V: J1.3, J2.VDD
+12V: C1.+, J1.1, J2.VMOT
DIR: J1.4, J2.DIR
GND: C1.-, J1.2, J2.GND, J2.GND@0 (GND), J4.2, J5.2, J6.2
unnamed: J2.MS1, J4.1
unnamed: J2.MS2, J5.1
unnamed: J2.MS3, J6.1
unnamed: J2.RST, J2.SLP (SLEEP)
unnamed: J2.2B, J3.1
unnamed: J2.1B, J3.4
unnamed: J2.1A, J3.3
unnamed: J2.2A, J3.2
STEP: J1.5, J2.STEP

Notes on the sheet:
Stepper Driver Module
V0.5 (02/06/2012)
(C) 2012 Luke Weston
Released under the CERN Open Hardware License: www.ohwr.org/cernohl
github.com/lukeweston/CNCPlotter

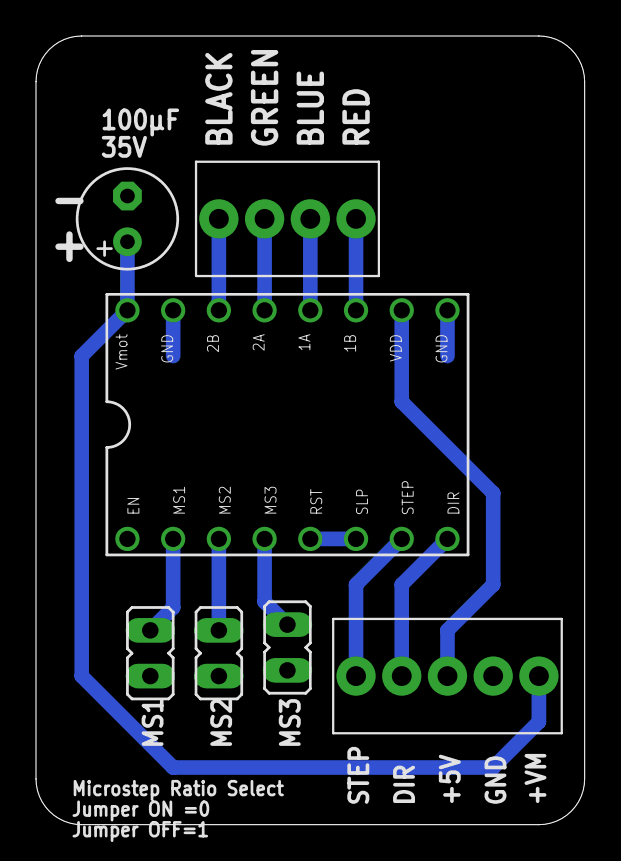
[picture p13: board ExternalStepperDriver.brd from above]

Board: 2 copper layers, 30.5 x 43.8 mm, 7 parts (0 on the bottom side), 13 nets.

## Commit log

2012-10-04 added BOM
2012-11-13 added external stepper module
    [ExternalStepperDriver.brd, ExternalStepperDriver.sch]
2013-01-05 added reset button
    [CNCPlotter.GBL, CNCPlotter.GBS, CNCPlotter.GTL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]
